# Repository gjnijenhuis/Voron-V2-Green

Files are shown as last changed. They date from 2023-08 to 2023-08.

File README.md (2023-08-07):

# klipper-backup 💾
Klipper backup script for manual or automated GitHub backups

This is a backup script to create manual or automated klipper backups in a github repository. You can [see an example](https://github.com/Staubgeborener/3dprint) of what it looks like in the end.

## RTFM
I would suggest reading the [wiki](https://github.com/Staubgeborener/klipper-backup/wiki), as this provides detailed step-by-step instructions.

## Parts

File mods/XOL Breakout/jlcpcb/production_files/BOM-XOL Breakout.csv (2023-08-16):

Comment | Designator | Footprint | LCSC
PICOBLADE_2-PIN_HEADER | PCF3,PCF4 | Molex_PicoBlade_53047-0210_1x02_P1.25mm_Vertical | C114130
Molex 43045-0200 | MCU2 | Molex_Micro-Fit_3.0_43045-0200_2x01_P3.00mm_Horizontal | C122431
JST-PH_4-PIN_HEADER | ESTEP1 | JST_PH_B4B-PH-K_1x04_P2.00mm_Vertical | C131334
JST-PH_2-PIN_HEADER | PCF1,PCF2 | JST_PH_B2B-PH-K_1x02_P2.00mm_Vertical | C131337
JST-PH_3-PIN_HEADER | FS1,HEF1,LED1,PROBE1 | JST_PH_B3B-PH-K_1x03_P2.00mm_Vertical | C131339
Molex 43650-0200 | HE0,TH0 | Molex_Micro-Fit_3.0_43650-0200_1x02_P3.00mm_Horizontal | C192562
Molex 43045-1400 | MCU1 | Molex_Micro-Fit_3.0_43045-1400_2x07_P3.00mm_Horizontal | C477050
FS 5V | JP13 | SolderJumper-2_P1.3mm_Open_TrianglePad1.0x1.5mm
FS 12V | JP12 | SolderJumper-2_P1.3mm_Open_TrianglePad1.0x1.5mm
FS 24V | JP11 | SolderJumper-2_P1.3mm_Open_TrianglePad1.0x1.5mm
PROBE 5V | JP10 | SolderJumper-2_P1.3mm_Open_TrianglePad1.0x1.5mm
PROBE 24V | JP8 | SolderJumper-2_P1.3mm_Open_TrianglePad1.0x1.5mm
PCF 5V | JP7 | SolderJumper-2_P1.3mm_Open_TrianglePad1.0x1.5mm
PCF 12V | JP6 | SolderJumper-2_P1.3mm_Open_TrianglePad1.0x1.5mm
PCF 24V | JP5 | SolderJumper-2_P1.3mm_Open_TrianglePad1.0x1.5mm
HEF 5V | JP4 | SolderJumper-2_P1.3mm_Open_TrianglePad1.0x1.5mm
HEF 12V | JP3 | SolderJumper-2_P1.3mm_Open_TrianglePad1.0x1.5mm
HEF 24V | JP2 | SolderJumper-2_P1.3mm_Open_TrianglePad1.0x1.5mm
AUX Select | JP1 | SolderJumper-3_P2.0mm_Open_TrianglePad1.0x1.5mm
M3 | H1 | MountingHole_3.2mm_M3_DIN965_Pad
M3 | H2 | MountingHole_3.2mm_M3_DIN965_Pad

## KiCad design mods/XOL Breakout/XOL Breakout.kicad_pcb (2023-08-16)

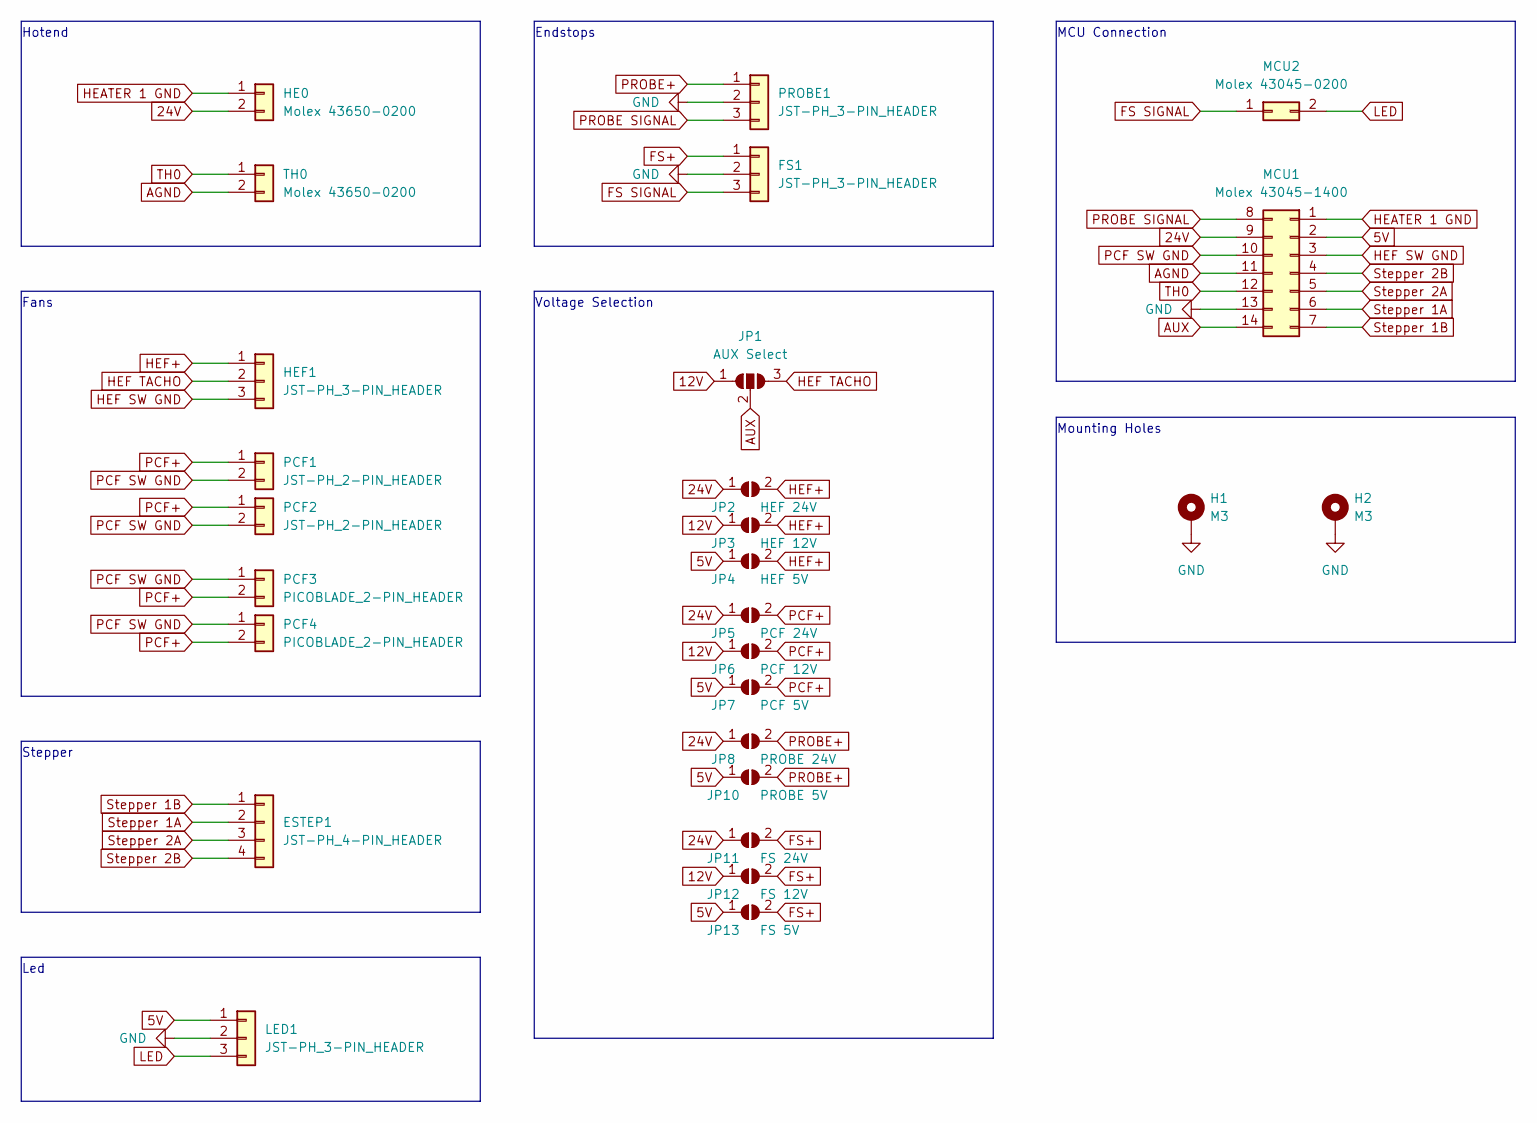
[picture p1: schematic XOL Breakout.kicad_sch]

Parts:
ESTEP1: JST-PH_4-PIN_HEADER; JST_PH_B4B-PH-K_1x04_P2.00mm_Vertical
FS1: JST-PH_3-PIN_HEADER; JST_PH_B3B-PH-K_1x03_P2.00mm_Vertical
H1, H2: M3; MountingHole_3.2mm_M3_DIN965_Pad
HE0: Molex 43650-0200; Molex_Micro-Fit_3.0_43650-0200_1x02_P3.00mm_Horizontal
HEF1: JST-PH_3-PIN_HEADER; JST_PH_B3B-PH-K_1x03_P2.00mm_Vertical
JP1: AUX Select; SolderJumper-3_P2.0mm_Open_TrianglePad1.0x1.5mm
JP2: HEF 24V; SolderJumper-2_P1.3mm_Open_TrianglePad1.0x1.5mm
JP3: HEF 12V; SolderJumper-2_P1.3mm_Open_TrianglePad1.0x1.5mm
JP4: HEF 5V; SolderJumper-2_P1.3mm_Open_TrianglePad1.0x1.5mm
JP5: PCF 24V; SolderJumper-2_P1.3mm_Open_TrianglePad1.0x1.5mm
JP6: PCF 12V; SolderJumper-2_P1.3mm_Open_TrianglePad1.0x1.5mm
JP7: PCF 5V; SolderJumper-2_P1.3mm_Open_TrianglePad1.0x1.5mm
JP8: PROBE 24V; SolderJumper-2_P1.3mm_Open_TrianglePad1.0x1.5mm
JP10: PROBE 5V; SolderJumper-2_P1.3mm_Open_TrianglePad1.0x1.5mm
JP11: FS 24V; SolderJumper-2_P1.3mm_Open_TrianglePad1.0x1.5mm
JP12: FS 12V; SolderJumper-2_P1.3mm_Open_TrianglePad1.0x1.5mm
JP13: FS 5V; SolderJumper-2_P1.3mm_Open_TrianglePad1.0x1.5mm
LED1: JST-PH_3-PIN_HEADER; JST_PH_B3B-PH-K_1x03_P2.00mm_Vertical
MCU1: Molex 43045-1400; Molex_Micro-Fit_3.0_43045-1400_2x07_P3.00mm_Horizontal
MCU2: Molex 43045-0200; Molex_Micro-Fit_3.0_43045-0200_2x01_P3.00mm_Horizontal
PCF1, PCF2: JST-PH_2-PIN_HEADER; JST_PH_B2B-PH-K_1x02_P2.00mm_Vertical
PCF3, PCF4: PICOBLADE_2-PIN_HEADER; Molex_PicoBlade_53047-0210_1x02_P1.25mm_Vertical
PROBE1: JST-PH_3-PIN_HEADER; JST_PH_B3B-PH-K_1x03_P2.00mm_Vertical
TH0: Molex 43650-0200; Molex_Micro-Fit_3.0_43650-0200_1x02_P3.00mm_Horizontal

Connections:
5V: JP4.1 (A), JP7.1 (A), JP10.1 (A), JP13.1 (A), LED1.1, MCU1.2
12V: JP1.1 (A), JP3.1 (A), JP6.1 (A), JP12.1 (A)
24V: HE0.2, JP2.1 (A), JP5.1 (A), JP8.1 (A), JP11.1 (A), MCU1.9
AGND: MCU1.11, TH0.2
AUX: JP1.2 (C), MCU1.14
FS SIGNAL: FS1.3, MCU2.1
FS+: FS1.1, JP11.2 (B), JP12.2 (B), JP13.2 (B)
GND: FS1.2, H1.1, H2.1, LED1.2, MCU1.13, PROBE1.2
HEATER 1 GND: HE0.1, MCU1.1
HEF SW GND: HEF1.3, MCU1.3
HEF TACHO: HEF1.2, JP1.3 (B)
HEF+: HEF1.1, JP2.2 (B), JP3.2 (B), JP4.2 (B)
LED: LED1.3, MCU2.2
PCF SW GND: MCU1.10, PCF1.2, PCF2.2, PCF3.1, PCF4.1
PCF+: JP5.2 (B), JP6.2 (B), JP7.2 (B), PCF1.1, PCF2.1, PCF3.2, PCF4.2
PROBE SIGNAL: MCU1.8, PROBE1.3
PROBE+: JP8.2 (B), JP10.2 (B), PROBE1.1
Stepper 1A: ESTEP1.2, MCU1.6
Stepper 1B: ESTEP1.1, MCU1.7
Stepper 2A: ESTEP1.3, MCU1.5
Stepper 2B: ESTEP1.4, MCU1.4
TH0: MCU1.12, TH0.1

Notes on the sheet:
MCU Connection
Endstops
Hotend
Mounting Holes
Led
Stepper
Fans
Voltage Selection

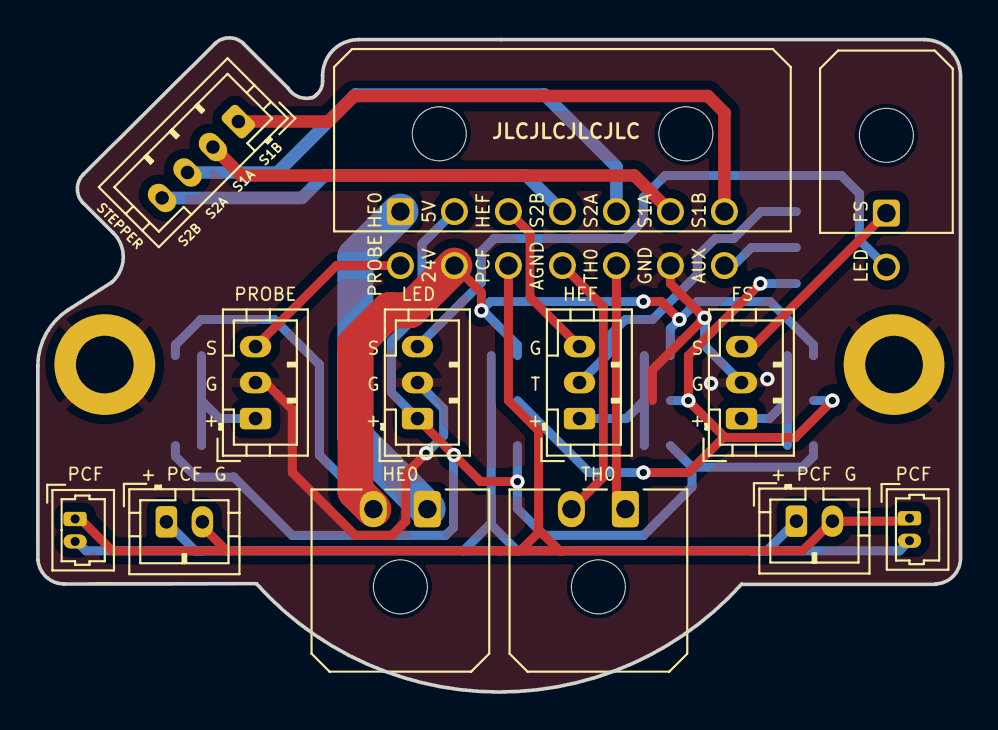
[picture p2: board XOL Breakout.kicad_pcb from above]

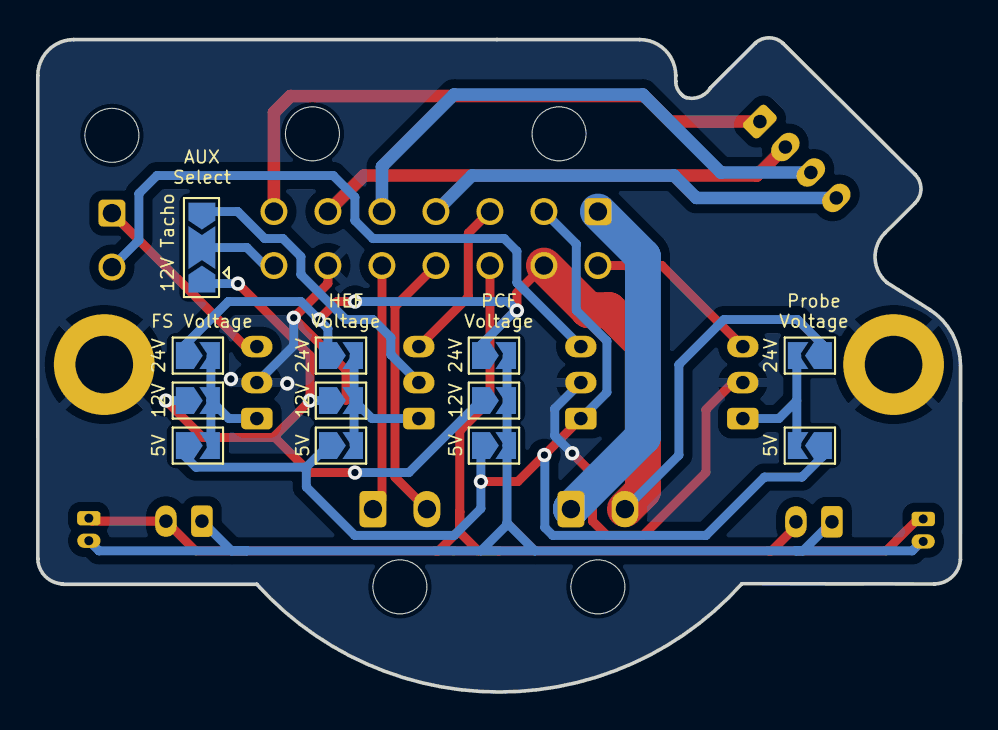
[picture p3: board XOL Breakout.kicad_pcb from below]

Board: 2 copper layers, 51.3 x 36.3 mm, 27 parts (12 on the bottom side), 22 nets.

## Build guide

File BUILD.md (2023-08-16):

# VORON GREEN

The Voron Green is a 300mm Voron 2.4, built around an LDO Kit ([LDO Motors Voron 2.4 300 Kit - 3DJake Nederland](https://www.3djake.nl/ldo-motors/voron-24-300-kit?sai=12016))

## Configuration

The basis of the configuration of Voron Green is done around Klippain. For further configuration details see the klipper folder in this repo.

[GitHub - Frix-x/klippain: Generic Klipper configuration for 3D printers](https://github.com/Frix-x/klippain)

## Mods

The following mods / adaptions have been made to make this printer even better:

### Display

The default graphic display is not very useful. On the voron green this has been replaced with a Waveshare 4.3" Touch Screen:

[Waveshare 4.3" Touch Screen on Amazon](https://www.amazon.nl/gp/product/B083Q8YLVP/)

This is mounted using the following mod:

[Touch Screen Mount on GitHub](https://github.com/VoronDesign/VoronUsers/tree/master/printer_mods/jeoje/4.3_Inch_Touchscreen_Mount)

**Note:** The new LDO revC kit already contains a nice 4.3" Touch Screen so no need to buy this one for future builds.

### Gantry Backers

On the Y extrusions gantry backers are installed to combat bending of the Y-Rails under temperature changes:

[Voron V2.4/Trident 300 Titanium Backers](https://lecktor.com/en/v2x-frames/1002-voron-v24trident-300-titanium-backers-01002.html)

**Note:** The X backer of this kit is not used as it is not needed on X due to the rail orientation. Installing this on top of the X extrusion will only make things worse!

### Kinematic Mount

To give the bed proper room for thermal expansion, without stress from the mounting a kinematic mount is used:

[Kinematic mount for V2.4](https://lecktor.com/en/v2x-buildplate/1032-kinematic-mount-for-v24-01032.html)

### Reinforced Gantry Mount

I don't like the way the gantry is mounted originally. I'm also not a huge fan (anymore) of the GE5C mod as it can have too much play. The Annex Reinforced Gantry mounts give a much more solid mounting of the gantry:

[Annex Reinforced Gantry Mounts](https://github.com/Annex-Engineering/Annex-Engineering_User_Mods/tree/main/Printers/Non_Annex_Printers/VORON_Printers/VORON_V2dot4/annex_dev-Reinforced_Gantry_Mounts)

[Needed ball end screws on Amazon](https://www.amazon.nl/dp/B07VYXTRL1)

### Front Idlers / Tensioners

On the Voron Green I'm using Rama's idlers:

[Rama's Idlers on GitHub](https://github.com/Ramalama2/Voron-2-Mods/tree/main/Front_Idlers)

However on a future build I would recommend the BFI (Beefy Front Idlers) from Clee as they are better:

[GitHub - clee/VoronBFI](https://github.com/clee/VoronBFI)

### Z Idlers / Tensioners

On the Voron Green I'm using the Z idlers from Hartk1213's pins mod:

[GitHub - Voron 2.4 Pins Mod](https://github.com/VoronDesign/VoronUsers/tree/master/printer_mods/hartk1213/Voron2.4_Trident_Pins_Mod)

However on a future build I would recommend the ZFI (Beefy Z Idlers) from Clee as they are better:

[GitHub - clee/VoronBFI](https://github.com/clee/VoronBFI)

### AB Motor Mounts

For the motor mounts the Hartk1213's pins mod is used:

[GitHub - Voron 2.4 Pins Mod](https://github.com/VoronDesign/VoronUsers/tree/master/printer_mods/hartk1213/Voron2.4_Trident_Pins_Mod)

### XY Joints and X-Beam

For the XY joints and X-Beam I've used the Trailhead from Armchair Engineering. This gives much more stiffness and reduces moving mass. I've used the 6mm / 1515 / MGN9 variant.

[GitHub - Armchair-Engineering/Trailhead-XY-Joints: Modified XY joints for the Voron 2.4 and Trident](https://github.com/Armchair-Engineering/Trailhead-XY-Joints)

For the X-Rail I've used a CPC rail from Fermio as we want the best possible rail on X as that is the only axis that is only constrained by 1 rail.

[Fermio - CPC MR 9ML 350mm](https://fermio.xyz/chieftek-precision-co.-ltd/cpc-mr-9ml-350-mm/)

### Toolhead

For the toolhead I'm using the XOL toolhead from Armchair Engineering. This is a stripped down toolhead, so the moving mass will be optimal, but still is very stiff.

[GitHub - Armchair-Engineering/Xol-Toolhead](https://github.com/Armchair-Engineering/Xol-Toolhead)

Along with the toolhead the following choices have been made:

#### Extruder

As extruder I'm using the Orbiter 2.0 as this one has the optimal balance between grip and motor torque. This one will skip steps instead of strip the filament when something goes wrong in the extrusion path. It also provides enough grip, as with some Glass Filled Nylons I've had issues getting good grip with the standard BMG gears of the StealthBurner. Don't go for the LGX lite. It has more grip, but at the cost of less torque.

[LDO Motors Orbiter Extruder V2.0 - 3DJake Nederland](https://www.3djake.nl/ldo-motors/orbiter-extruder-v20)

#### Hotend

For the hotend the Voron Green is using the Phasetus Rapido Plus (PT1000) in combination with Bondtech CHT bi-metal nozzles. This gives the best possible flow rate.

I did not choose to go with the E3D Revo. The Revo has issues with the heatbreak bending, and also does not have a high flow nozzle for abbraisive filaments.

[Phaetus Rapido Plus Hotend HF - 3DJake Nederland](https://www.3djake.nl/phaetus/rapido-plus-hotend-hf)

[BondTech CHT BiMetal RepRap Nozzle - 3DJake Nederland](https://www.3djake.nl/bondtech/cht-bimetal-reprap-nozzle?sai=14008)

#### Toolhead PCB

For the toolhead PCB I'm using a custom PCB that uses the pinout of the Stealthburner PCB so the existing wiring of the LDO kit can be re-used. The custom PCB has the options to wire 12V to the fans, which is needed when the Delta Fans are used for the XOL Toolhead.

[GitHub - XOL PCB](mods/XOL%20Breakout)

#### Z-Probe

The Voron Green uses the Euclid Z-Probe. Kicky PCB is a good alternative. Avoid the normal Klicky or Klicky-NG as they are not as stable.

[Lecktor - Euclid probe](https://lecktor.com/en/sensors/1143-euclid-probe-01143.html)

[Printables - Euclid Gantry Dock with Magnet](https://www.printables.com/model/388004-longer-euclid-dock-arm-with-magnet-for-retention)

### Z-Endstop

The Sexbolt mod is used as Z-Endstop as this gives the best force on the nozzle to squeeze away any plastic before probing.

[Z endstop Sexbolt - Lab4450.com](https://lab4450.com/product/z-endstop-sexbolt/)

### Front Door

I personally don't like the double front doors of the original Voron, so I instead went with a 6mm thick, single panel door:

[GitHub - BeunHaas34 Annex Door](https://github.com/Annex-Engineering/Annex-Engineering_User_Mods/tree/main/Printers/Redoubt/BeunHaas34-Annex_Door)

However recently a new mod was released with an even sturdier door. You might want to consider this one for future builds:

[GitHub - Whopping Clicky Clacky Door](https://github.com/tanaes/whopping_Voron_mods/tree/main/clickyclacky_door)

### Panel Mounts

I'm using Annex's panel mounts as they make it so much easier to remove the panels.

[GitHub - Annex Panel Clips](https://github.com/Annex-Engineering/Annex-Engineering_User_Mods/tree/main/Printers/All_Printers/annex_dev-Panel_2020_Clips_and_Hinges)

### Purge Bucket

The following purge bucket / nozzle brush holder / plate stopper is used. You can use the nozzle brush from the LDO kit with this one:

[GitHub - Decontaminator Purge Bucket & Nozzle Scrubber](https://github.com/VoronDesign/VoronUsers/tree/master/orphaned_mods/printer_mods/edwardyeeks/Decontaminator_Purge_Bucket_%26_Nozzle_Scrubber)

### Camera

A Logitech C920 camera is mounted on the top of the gantry using this mod:

[GitHub - Voron 2.4 C920 Mount](https://github.com/VoronDesign/VoronUsers/tree/master/printer_mods/Koios/C920_Mount)

### Umbilical

The X/Y cable chains have been removed. It adds weight and is not supported with the XOL toolhead and/or TrailHead 1515 XY Joints. The XOL toolhead natively supports the umbilical, but the following mod is used on the A motor drive to support the umbilical:

[Printables - Voron V2.4 Rear Umbilical](https://www.printables.com/model/363657-voron-v24-rear-umbilical)

Note that the Voron Green uses sensorless homing, so no need to print anything related to the endstops.

### Filament Sensor

The BTT filament sensor (REV1) is used to sense movement of filament. This will detect filament runout as well as filament blockage.

[Amazon - BTT SFS](https://www.amazon.nl/dp/B089NYC6JL)

The sensor is mounted at the rear top of the Voron with a modified exhaust cover:

[GitHub - Voron Exhaust Cover for BTT SFS](https://github.com/VoronDesign/VoronUsers/tree/master/printer_mods/Fiction/Exhaust_cover_SFS)

### Extra Thermistors

Two extra thermistors are mounted in Voron Green:

- In the Z Cable chain to measure chamber temperature

- In the rear right Z extrusion to measure frame temperature

### ADXL

Nozzle mount accelerometer gives the best results for input shaper. To use the LDO ADXL board in this way I'm using the Nozzle Mount adapter (using an M6 bolt to hard fasten it to the hotend):

[GitHub - Armchair Engineering's Rapido ADXL Nozzle Thread Mount](https://github.com/Armchair-Engineering/ADXL-Mounts/blob/main/STLs/RapidoADXL_v14%20-%20Nozzle%20Thread%20Mount.stl)

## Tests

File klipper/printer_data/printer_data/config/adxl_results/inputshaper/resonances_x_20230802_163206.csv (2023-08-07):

freq | psd_x | psd_y | psd_z | psd_xyz
0.0 | 4.677e+03 | 5.568e+01 | 5.938e+00 | 4.739e+03
1.6 | 3.248e+03 | 5.674e+01 | 2.299e+01 | 3.327e+03
3.1 | 5.751e+02 | 2.798e+01 | 2.541e+01 | 6.285e+02
4.7 | 1.821e+03 | 2.999e+01 | 2.407e+01 | 1.875e+03
6.2 | 5.197e+03 | 4.083e+01 | 2.473e+01 | 5.262e+03
7.8 | 8.405e+03 | 5.394e+01 | 2.385e+01 | 8.483e+03
9.3 | 1.192e+04 | 6.589e+01 | 2.570e+01 | 1.202e+04
10.9 | 1.622e+04 | 8.303e+01 | 2.590e+01 | 1.633e+04
12.4 | 2.143e+04 | 9.970e+01 | 2.709e+01 | 2.155e+04
14.0 | 2.749e+04 | 1.198e+02 | 2.582e+01 | 2.764e+04
15.6 | 3.507e+04 | 1.583e+02 | 2.646e+01 | 3.525e+04
17.1 | 4.541e+04 | 2.274e+02 | 2.734e+01 | 4.567e+04
18.7 | 6.028e+04 | 4.077e+02 | 2.569e+01 | 6.072e+04
20.2 | 6.079e+04 | 4.569e+02 | 2.660e+01 | 6.127e+04
21.8 | 5.249e+04 | 3.546e+02 | 3.028e+01 | 5.288e+04
23.3 | 6.324e+04 | 8.887e+02 | 4.244e+01 | 6.417e+04
24.9 | 7.873e+04 | 8.574e+02 | 3.370e+01 | 7.962e+04
26.4 | 9.572e+04 | 6.866e+02 | 2.552e+01 | 9.643e+04
28.0 | 1.139e+05 | 7.323e+02 | 2.563e+01 | 1.147e+05
29.5 | 1.274e+05 | 6.794e+02 | 2.716e+01 | 1.281e+05
31.1 | 1.396e+05 | 5.710e+02 | 3.238e+01 | 1.402e+05
32.7 | 1.620e+05 | 5.949e+02 | 3.312e+01 | 1.627e+05
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

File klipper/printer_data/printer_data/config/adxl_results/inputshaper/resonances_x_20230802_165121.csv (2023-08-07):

freq | psd_x | psd_y | psd_z | psd_xyz
0.0 | 4.570e+03 | 3.636e+01 | 7.517e+00 | 4.614e+03
1.6 | 2.757e+03 | 4.224e+01 | 2.431e+01 | 2.823e+03
3.1 | 3.736e+02 | 3.156e+01 | 2.563e+01 | 4.307e+02
4.7 | 1.709e+03 | 3.687e+01 | 2.471e+01 | 1.770e+03
6.2 | 5.096e+03 | 4.562e+01 | 2.175e+01 | 5.163e+03
7.8 | 8.204e+03 | 5.676e+01 | 2.213e+01 | 8.283e+03
9.3 | 1.172e+04 | 7.446e+01 | 2.428e+01 | 1.182e+04
10.9 | 1.590e+04 | 8.593e+01 | 2.631e+01 | 1.602e+04
12.4 | 2.105e+04 | 1.028e+02 | 2.830e+01 | 2.118e+04
14.0 | 2.726e+04 | 1.295e+02 | 2.734e+01 | 2.742e+04
15.6 | 3.464e+04 | 1.643e+02 | 2.499e+01 | 3.483e+04
17.1 | 4.416e+04 | 2.216e+02 | 2.552e+01 | 4.441e+04
18.7 | 5.885e+04 | 3.762e+02 | 2.520e+01 | 5.925e+04
20.2 | 6.457e+04 | 5.280e+02 | 2.749e+01 | 6.512e+04
21.8 | 5.173e+04 | 3.248e+02 | 3.328e+01 | 5.208e+04
23.3 | 6.083e+04 | 7.440e+02 | 4.930e+01 | 6.162e+04
24.9 | 7.633e+04 | 8.568e+02 | 3.816e+01 | 7.722e+04
26.4 | 9.378e+04 | 6.941e+02 | 2.515e+01 | 9.449e+04
28.0 | 1.118e+05 | 7.506e+02 | 2.405e+01 | 1.125e+05
29.5 | 1.265e+05 | 7.244e+02 | 2.421e+01 | 1.272e+05
31.1 | 1.384e+05 | 5.681e+02 | 2.731e+01 | 1.390e+05
32.7 | 1.600e+05 | 5.909e+02 | 2.775e+01 | 1.607e+05
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

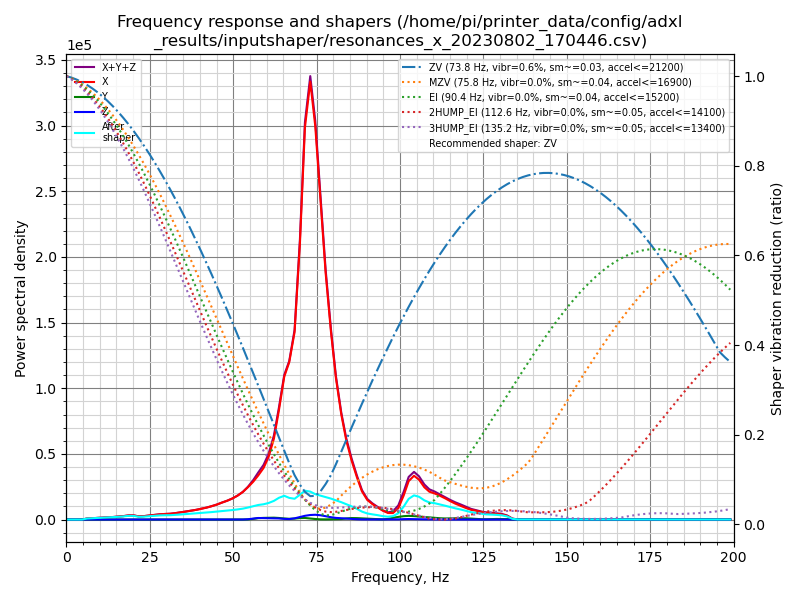
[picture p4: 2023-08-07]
klipper/printer_data/printer_data/config/adxl_results/inputshaper/resonances_x_20230802_170446.png

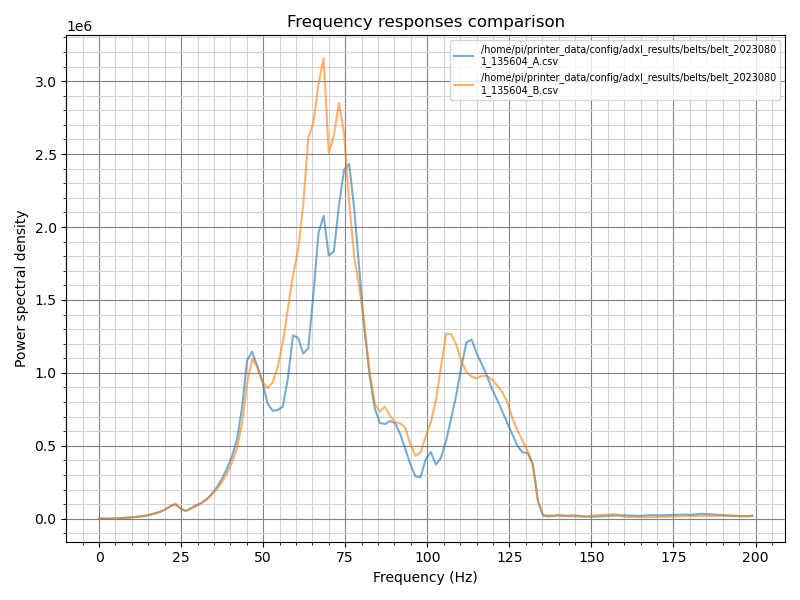
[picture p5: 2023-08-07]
klipper/printer_data/printer_data/config/adxl_results/belts/belts_20230801_135604.png

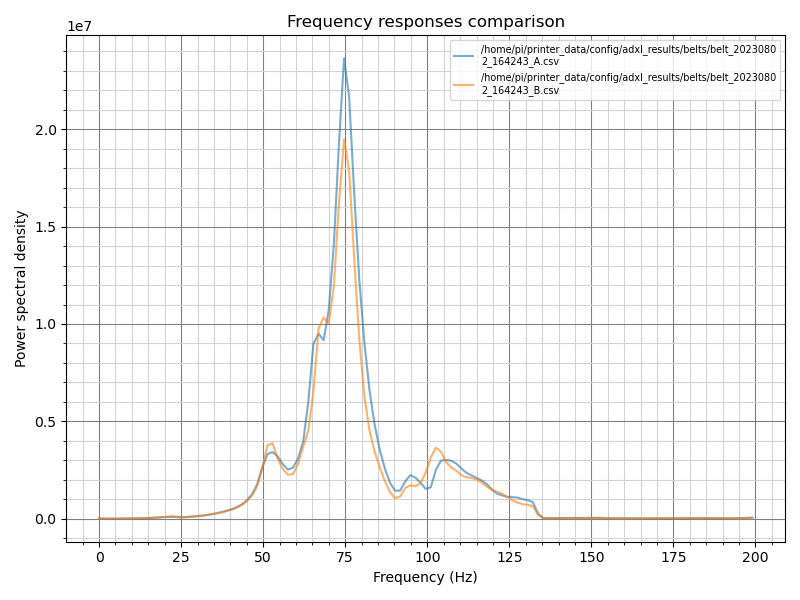
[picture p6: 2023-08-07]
klipper/printer_data/printer_data/config/adxl_results/belts/belts_20230802_164243.png

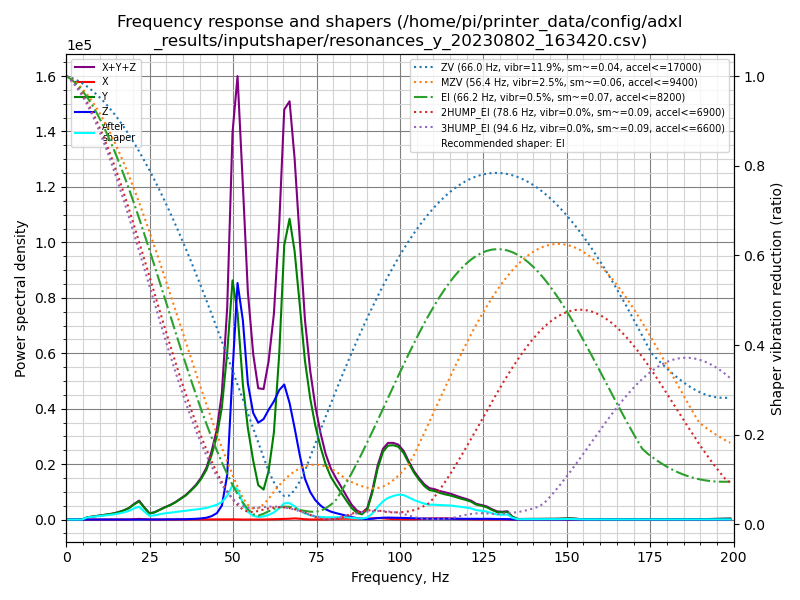
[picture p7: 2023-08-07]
klipper/printer_data/printer_data/config/adxl_results/inputshaper/resonances_y_20230802_163420.png

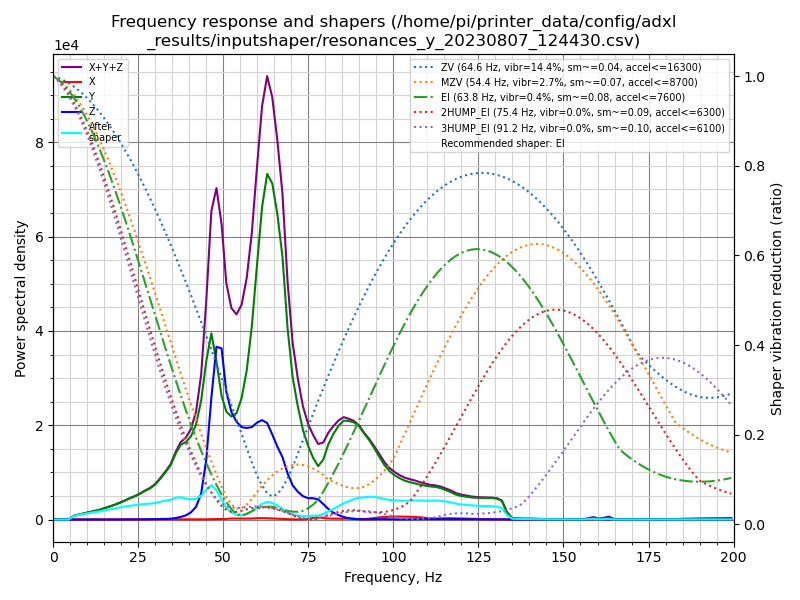
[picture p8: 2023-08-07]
klipper/printer_data/printer_data/config/adxl_results/inputshaper/resonances_y_20230807_124430.png

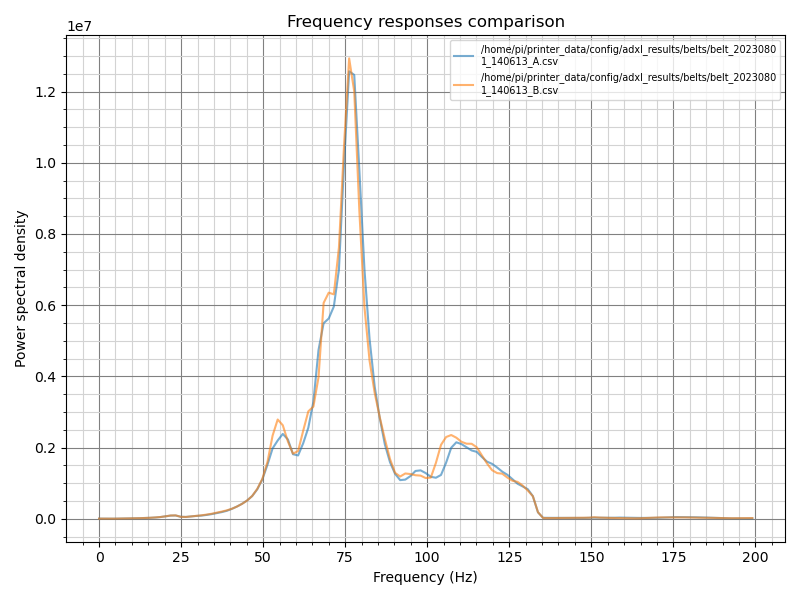
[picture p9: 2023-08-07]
klipper/printer_data/printer_data/config/adxl_results/belts/belts_20230801_140613.png

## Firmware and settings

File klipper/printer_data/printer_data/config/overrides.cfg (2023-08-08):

############################################# \
######## USER CONFIG OVERRIDES FILE #########  + --> This will help you personalize my config to your printer :)
############################################# /

# This file is yours! Feel free to edit it in order to include all the needed
# things to adapt my generic config to your machine. This file will not be erased
# when updating the config using moonraker and it will be kept as you've set it.
# You can change every section of the config. You can also add some new custom macros, etc...
# The corresponding documentation can be found in: docs > overrides.md

### Also, keep in mind: if you use a multi-MCU config such as the old school double SKRs or a CANbus toolhead
### board, you will need to specify which components are connected to which board in your own mcu.cfg file!
### Example: if something is connected to the toolhead MCU, you should use "config_pin: toolhead:PIN_NAME".

#> Main control MCUs are called "mcu" (and "secondary" when using a double MCU configuration)
#> Toolhead CANboard MCUs are called "toolhead"
#> ERCF MCUs are called "ercf" 

# ------------------------------------------------------------------------------------------


#-------------------------#
#   START_PRINT SEQUENCE  #
#-------------------------#

## The START_PRINT sequence is modular and fully customizable. A default START_PRINT sequence is auto-populated based on
## your probe choice (TAP, Dockable, Inductive), but if for some reasons you still want to modify it, please uncomment the following 3
## lines to define a new `variable_startprint_actions`. You can use any number of action or even duplicate some actions if needed.
## Available actions: "bed_soak", "extruder_preheating", "chamber_soak", "extruder_heating", "tilt_calib", "z_offset", "bedmesh", "purge", "clean", "primeline"
##
# [gcode_macro _USER_VARIABLES]
# variable_startprint_actions: "action1", "action2", ...
# gcode: # do not remove this line

#-------------------------#
#   KINEMATICS            #
#-------------------------#
[printer]
max_velocity: 400
max_accel: 20000
max_z_velocity: 30
max_z_accel: 500
square_corner_velocity: 10.0

#-------------------------#
#   INPUT SHAPER          #
#-------------------------#
[resonance_tester]
accel_per_hz: 150
hz_per_sec: 0.5

[input_shaper]
# Supported shapers: zv, mzv, zvd, ei, 2hump_ei, 3hump_ei
shaper_freq_x: 70.6
shaper_type_x: mzv
shaper_freq_y: 54.4
shaper_type_y: mzv

#-------------------------#
#   EXTRUDER/BED          #
#-------------------------#

[extruder]
dir_pin: !E_DIR
rotation_distance: 4.637
gear_ratio: 1:1
control: pid
pid_kp: 26.015
pid_ki: 1.770
pid_kd: 95.603
sensor_type: PT1000
min_temp: 10
max_temp: 320
max_power: 1.0
min_extrude_temp: 170

[tmc2209 extruder]
run_current: 0.65

[heater_bed]
control: pid
pid_kp: 38.771
pid_ki: 1.746
pid_kd: 215.177

#-------------------------#
#   FANS                  #
#-------------------------#

[heater_fan hotend_fan]
tachometer_pin: ^E_FAN_TACHO
tachometer_ppr: 2
tachometer_poll_interval: 0.00015

#-------------------------#
#   Z Steppers            #
#-------------------------#
[stepper_z1]
dir_pin: !Z1_DIR

[stepper_z3]
dir_pin: !Z3_DIR

[autotune_tmc stepper_z]
motor: ldo-42sth48-2004ac
[autotune_tmc stepper_z1]
motor: ldo-42sth48-2004ac
[autotune_tmc stepper_z2]
motor: ldo-42sth48-2004ac
[autotune_tmc stepper_z3]
motor: ldo-42sth48-2004ac

#-------------------------#
#   XY Steppers           #
#-------------------------#
[stepper_x]
homing_speed: 40  
homing_retract_dist: 0
homing_positive_dir: true
position_min: 0
position_endstop: 295
position_max: 295

[stepper_y]
homing_speed: 40  
homing_retract_dist: 0
homing_positive_dir: true
position_min: 0
position_endstop: 308
position_max: 308

[tmc2209 stepper_x]
run_current: 1.2

[tmc2209 stepper_y]
run_current: 1.2

[autotune_tmc stepper_x]
motor: ldo-42sth48-2004mah
sg4_thrs: 140

[autotune_tmc stepper_y]
motor: ldo-42sth48-2004mah
sg4_thrs: 140

#-------------------------#
#   LEDs                  #
#-------------------------#
[gcode_macro _USER_VARIABLES]
variable_status_leds_logo_idx: '2'
variable_status_leds_nozzle_idx: '1,3'

[output_pin caselight]
cycle_time: 0.001

#-------------------------#
#   STARTUP               #
#-------------------------#
[gcode_macro _INIT_USERCUSTOM]
gcode:
    STATUS_LEDS COLOR="READY"
    LIGHT_ON

#-------------------------#
#   Z CALIBRATION         #
#-------------------------#
[z_calibration]
# Physical Z endstop pin position
nozzle_xy_position: 94.3,305
# Probe switch position on physical endstop
switch_xy_position: 99,275
# Switch offset (default D2F-5: 0.5mm and SSG-5H: 0.7mm)
# Smaller number means higher nozzle to the PEI
switch_offset: 0.50
offset_margins: -0.750, 1.0


#-------------------------#
#   OVERIDES              #
#-------------------------#
[include overrides/config/software/thermal_adjust.cfg]
[include overrides/macros/helpers/fan_tach_monitor.cfg]
[include overrides/macros/helpers/update_git.cfg]
[include overrides/macros/helpers/prime.cfg]
[include overrides/macros/calibration/test_speed.cfg]
[include overrides/macros/hardware_functions/filter.cfg]

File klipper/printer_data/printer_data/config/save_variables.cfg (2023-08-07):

[Variables]
ercf_calib_0 = 1.0
ercf_calib_1 = 1.0
ercf_calib_2 = 1.0
ercf_calib_3 = 1.0
ercf_calib_4 = 1.0
ercf_calib_5 = 1.0
ercf_calib_6 = 1.0
ercf_calib_7 = 1.0
ercf_calib_8 = 1.0
ercf_calib_9 = 1.0
ercf_calib_10 = 1.0
ercf_calib_11 = 1.0
ercf_calib_ref = 500.0
ercf_calib_clog_length = 8.0

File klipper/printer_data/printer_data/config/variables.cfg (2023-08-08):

[gcode_macro _USER_VARIABLES]
# Enable verbose output to let the macro have a chat
variable_verbose: True

###################################################
# Feedrate and accels setpoints for all the macros
###################################################

## SPEEDS
variable_homing_travel_speed: 350
variable_travel_speed: 350
variable_z_drop_speed: 15
variable_brush_clean_speed: 100
variable_probe_dock_speed: 60

## ACCELS
## Those are specific accel settings for some of the macros
variable_homing_travel_accel: 10000
variable_tilting_travel_accel: 10000
variable_brush_clean_accel: 10000
variable_probe_dock_accel: 2000

## Accel to decel scale factor (default is 75% of the accel)
variable_accel_to_decel_factor: 0.75


#################################################
# Homing, start_print and end_print variables
#################################################

## Physical Z endstop pin position. This variable is used only if
## you don't use the automatic z_calibration plugin: if this plugin is
## installed, the z endstop pin position is directly extracted from the
## plugin config file (see config/software/z_calibration.cfg) or its user override.
variable_zendstop_position: -1, -1 # change it ONLY if not using the auto z calibration plugin !!!

## Force always a full homing and QGL/Z_TILT during the START_PRINT macro
variable_force_homing_in_start_print: False

## Z hop before homing to avoid grinding
## the bed due to the gantry sag
variable_homing_zhop: 5

## XY axis homing order and backoff distance after touching the endstops
variable_homing_first: "X" # can be set to "Y" first
variable_homing_backoff_distance_xy: -5, -5 # move 5mm in negative direction on both axis

## Percentage of run_current used while sensorless homing (if used)
variable_sensorless_current_factor: 41

## margin to avoid the probe dock when homing
variable_probe_dock_margin_xy: 0, 0

## Temperature of the extruder used to preheat the chamber temperature and do some START_PRINT actions
variable_safe_extruder_temp: 150

## Prime line parameters
variable_prime_line_xy: 5, 2.5 # starting point
variable_prime_line_direction: "X" # can also be set to "Y"
variable_prime_line_length: 40 # length of the prime line on the bed (in mm)
variable_prime_line_purge_distance: 30 # length of filament to purge (in mm)
variable_prime_line_flowrate: 10 # mm3/s used for the prime line

## Park position used when pause, end_print, etc...
variable_park_position_xy: 295, 308
variable_park_lift_z: 50

## Automatically disable motors in the END_PRINT macro
variable_disable_motors_in_end_print: False

## Automatically turn-off heaters in the END_PRINT macro
variable_turn_off_heaters_in_end_print: True


#########################################################
# Dockable probe variables (if available in the machine)
#########################################################

## Bed size used to avoids doing a probe_accuracy or probe_calibrate outside the bed
## This has no effect in the macros beside a safety check (not mandatory to be changed)
variable_min_bed_xy: 0, 0
variable_max_bed_xy: 295, 300

## Minimum safe Z height to attach/detach probe
variable_probe_min_z_travel: 20

## Position of the probe dock
variable_probe_dock_location_xy: 0, 300

## Servo angles used to define the retracted and deployed positions
## of the dock (if applicable). These variables are only used if a probe servo
## is included in the config and have no effect if it's not the case
variable_probe_servo_angle_retracted: 0
variable_probe_servo_angle_deployed: 90

## Positions of the toolhead when docking/undocking the probe
## See diagram below for help
variable_probe_before_attach_position: "front"
variable_probe_after_attach_position : "right"
variable_probe_before_dock_position : "right" # generaly same as probe_after_attach_position
variable_probe_after_dock_position : "front"

variable_probe_move_attach_length: 50
variable_probe_move_dock_length: 50

##    Y
##    ^ 
##    |          back
##    |           ^
##    |   left  < O >  right
##    |           v
##    |         front
##    |_ _ _ _ _ _ _ _ _ _ _ _> X

## If there is an error during a tilting procedure (QGL or Z_TILT_ADJUST) or during a BED_MESH_CALIBRATE
## then automatically dock the probe before stopping all actions. This avoid letting the probe
## very close to a very hot bed doing nothing as this could destroy the probe microswitch
variable_autodock_on_probe_error: True


##########################################################
# Voron TAP probe variables (if available in the machine)
##########################################################

variable_tap_max_probing_temp: 150
variable_tap_deactivation_zhop: 5 # this is used to Z hop before restoring the temperature to avoid burnt PEI


##########################################
# Material and specific print parameters
##########################################

## default START_PRINT parameters
variable_print_default_bed_temp: 105
variable_print_default_extruder_temp: 240
variable_print_default_chamber_temp: 0
variable_print_default_chamber_max_heating_time: 15
variable_print_default_soak: 8
variable_print_default_material: "XXX"

## Material configuration parameters applied during START_PRINT by using the slicer MATERIAL variable
## FYI, retract paramaters are used only if firmware retraction is enabled, filter speed (in %) is used if
## there is a filter installed on the machine, etc...
## If you are using another material, just extend the list bellow with a new material and everything should work :)
variable_material_parameters: {
        'PLA': {
            'pressure_advance': 0.0525,
            'retract_length': 0.75,
            'unretract_extra_length': 0,
            'retract_speed': 40,
            'unretract_speed': 30,
            'filter_speed': 0,
            'additional_z_offset': 0
        },
        'PET': {
            'pressure_advance': 0.0650,
            'retract_length': 1.4,
            'unretract_extra_length': 0,
            'retract_speed': 30,
            'unretract_speed': 20,
            'filter_speed': 0,
            'additional_z_offset': 0.020
        },
        'ABS': {
            'pressure_advance': 0.0480,
            'retract_length': 0.5,
            'unretract_extra_length': 0,
            'retract_speed': 40,
            'unretract_speed': 30,
            'filter_speed': 80,
            'additional_z_offset': 0
        },
        'ASA': {
            'pressure_advance': 0.0480,
            'retract_length': 0.5,
            'unretract_extra_length': 0,
            'retract_speed': 40,
            'unretract_speed': 30,
            'filter_speed': 80,
            'additional_z_offset': 0
        }
    }


################################################
## ERCF specific variables
################################################
## This section is only considered if an ERCF is installed and configured

variable_ercf_unload_on_cancel_print: False
variable_ercf_unload_on_end_print: True
variable_ercf_reset_stats_on_start_print: False


################################################
# Other hardware options used in the macros
################################################

## Brush and purge bucket available in the machine
## If this is not available in the machine, set both positions
## variables to "-1, -1, -1" for safety
variable_purge_and_brush_enabled: True
variable_force_homing_before_brush: False # Add an homing of the Z axis before a clean to be sure to not miss the brush
variable_brush_over_y_axis: True # Cleanup is done moving the extruder along the Y axis, then X axis. If false, only X axis is done
variable_brush_xyz: 222, 308, 0 # Position of the brush center for nozzle cleaning
variable_purge_bucket_xyz: 275, 308, 0 # Purge bucket position
variable_purge_distance: 30 # Amount to purge (in mm)
variable_purge_ooze_time: 10 # Time (in seconds) to wait after the purge to let the nozzle ooze before going to the brush

## Servo angles used to define the retracted and deployed positions
## of the purge bucket and brush (if applicable). These variables are only used if a purge
## bucket servo is included in the config and have no effect if it's not the case
variable_purgeclean_servo_angle_retracted: 0
variable_purgeclean_servo_angle_deployed: 90


## White light parameters (if installed in the machine)
variable_light_intensity_start_print: 100
variable_light_intensity_printing: 30
variable_light_intensity_end_print: 30


## Patch the M190/M109 commands to avoid some wait time while the temperature
## settle on very low thermal latency devices (such as the BambuLabs hotend)
variable_fix_heaters_temperature_settle: False


## Resonnance testing position (if an accelerometer is installed in the machine)
## If test point is let to -1,-1, it default to the center of the bed at 50mm high
variable_resonnance_test_point_xy: -1, -1
variable_resonnance_test_z_clearance: 50
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

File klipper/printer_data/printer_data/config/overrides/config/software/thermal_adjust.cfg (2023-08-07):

[thermistor 100k3950_airtemp]
temperature1: 20
resistance1: 125245
temperature2: 50
resistance2: 35900
temperature3: 80
resistance3: 12933

[z_thermal_adjust]
temp_coeff: 0.0009
sensor_type: 100k3950_airtemp
sensor_pin: ZTHERMAL_THERMISTOR
min_temp: 0
max_temp: 200

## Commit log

2023-08-07 New backup from 07-08-23
    [XY.cfg, fan_tach_monitor.cfg, homing.cfg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]
2023-08-08 New backup from 08-08-23
    [overrides.cfg, prime.cfg, printer.cfg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]
2023-08-16 Added XOL PCB to the repo
    [BOM-XOL Breakout.csv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]
2023-08-16 Update BUILD.md
    Added XOL PCB link to the build file
